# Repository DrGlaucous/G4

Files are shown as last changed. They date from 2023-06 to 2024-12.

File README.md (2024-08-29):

# "Governor" G4

This is a repo for a low-cost and feature-rich "flywheel-type" nerf blaster.

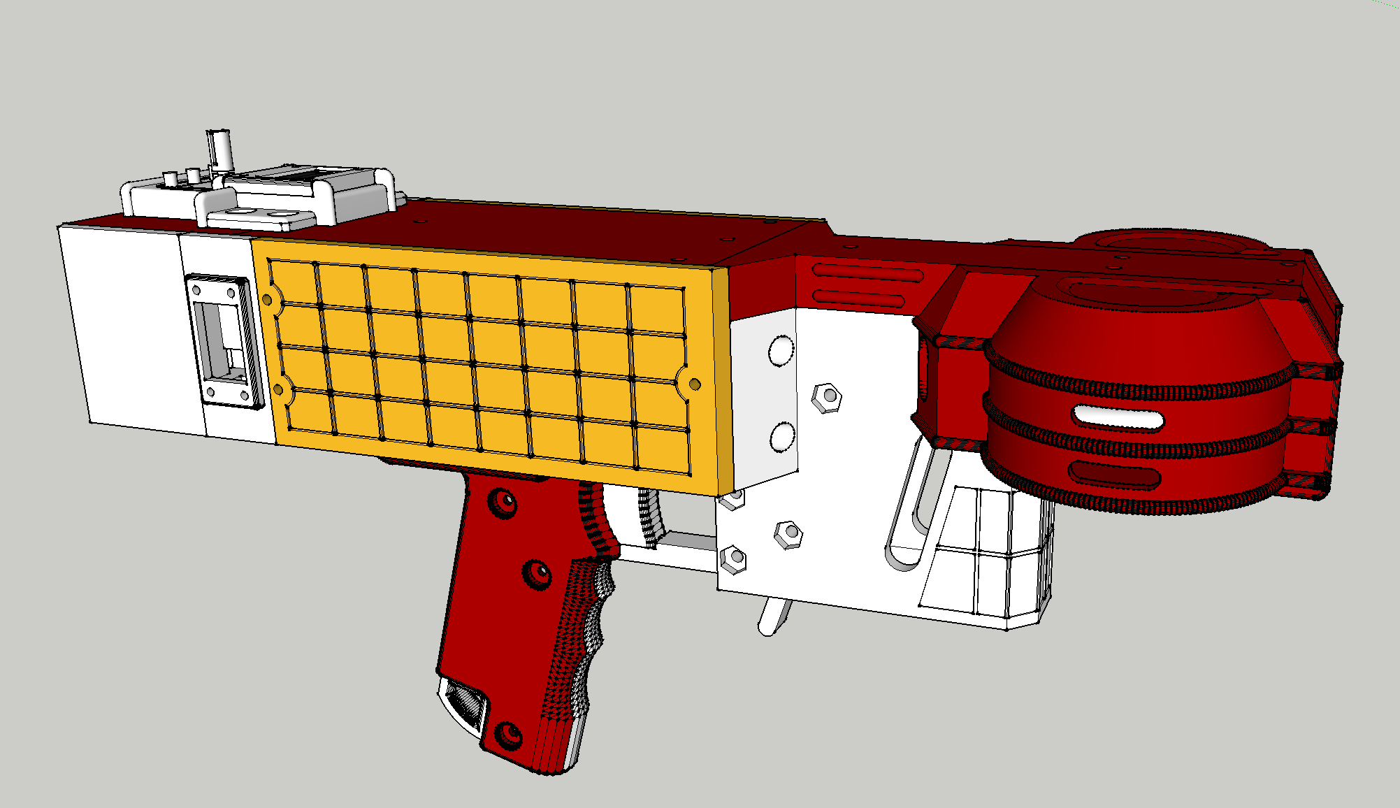
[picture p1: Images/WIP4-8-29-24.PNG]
Rendering of current iteration


Features/Speficications:
- Goal build cost < 150$
- Minimal plastic-anchored screws *(almost evertthing is secured with bolts + captive nuts)*
- Brushless motor flyhweels
- Solenoid pusher
- LCD display
- Angled talon compatability *(straight stick support planned)*
- Integrated ammo counter hardware
- Integrated chronograph hardware
- 3-5S Lipo compatable
- 6cm flywheel diameter
- ESP32 controller
- Closed-loop flywheel control (providing fixed RPM and fast spinup times)
- Through-hole electronics and soldering
- Fast decay solenoid driver

Many of these features are implemented in the G4's companion firmware, [Detty](https://github.com/DrGlaucous/DettyFW).

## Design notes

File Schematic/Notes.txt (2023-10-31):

Potential MOSFET for use with ESP32:

From Mouser:
IPP030N06NF2SAKMA1	3.05mh	3.3v thresh	1.52$	(large package only)
TK4R3A06PL,S4X	3.3mh	1.5vThresh	disp: 1.616Watt
TK4R3E06PL	3.3mh	1.5vThresh	disp: 1.616Watt (same as above, but better) 1.45$	(large package only)
IRFB3306/IRFSL3306PBF 	3.3-4.2mh	2-4vThresh	1.8$	(desirable package not stocked)
IPP019N06NF2S	1.9mh	3.3vthresh	2.1$	(large package only)
IRLB3034 ? (1.7mh), but 40vmax	$3.7$
IRFB3077	3.3mh	2-4vThresh	disp: 0.5925W with lowest (max: 2.4W)	2.2$

Pfet driver:
2N7000: Nfet, several ohm RDSon, but we won't pull much current through it.

P channel:
IPP120P04P4L03AKSA2	3.1mh	5vthresh	40vmax	$3.61

calculate dissipated power: I * I * Rds
calculate jnctn temp: multiply that by 50/60 degC/watt

at 20 volts on 1.5 ohms (solenoid), 13.33 amps flow

Choice:
DigiKey electronincs:
G040P04T - p channel (x5) $1.82/pc || https://www.digikey.com/en/products/detail/goford-semiconductor/G040P04T/19524542
or
G75P04T - p channel (x5) $1.18/pc || https://www.digikey.com/en/products/detail/goford-semiconductor/G75P04T/18768879
or
G050P03T - p channel (x5) $1.17/pc || https://www.digikey.com/en/products/detail/goford-semiconductor/G050P03T/18087996

25WA470MEFCT810X9 capacitor, 25v 470uf (x10) $0.43/pc || https://www.digikey.com/en/products/detail/rubycon/25WA470MEFCT810X9/3566890

CSD18532KCS - n channel (x5) $2.31/pc || https://www.digikey.com/en/products/detail/texas-instruments/CSD18532KCS/3661861
or cheap:
IRLB8314PBF - n channel (x5) $1.00/pc || https://www.digikey.com/en/products/detail/infineon-technologies/IRLB8314PBF/4807868 **
or (not as good...)
IRLB8748PBF 0.0068 - 2.35 - n cnannel (x5) $1.05/pc || https://www.digikey.com/en/products/detail/infineon-technologies/IRLB8748PBF/2127672
IRL7833PBF 0.0045 - 2.30 - 1.85 || https://www.digikey.com/en/products/detail/infineon-technologies/IRL7833PBF/811242

ordered:
G75P04T - pch
25WA470MEFCT810X9 - cap
IRLB8314PBF - nch

Mouser electronics (bad cap selection):
IPP030N06NF2SAKMA1- N channel (x10)
IPP120P04P4L03AKSA2 - P channel (x3)
870585375004 - Cap, 470 uf (x2) (1mc cubed footprint, 5mm leads)

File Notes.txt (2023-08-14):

Useful info:
https://randomnerdtutorials.com/esp32-pinout-reference-gpios/

how to wire and use a 2 pin IR photodiode:
https://youtu.be/_mOF1JXo1DU
https://forum.arduino.cc/t/2-pin-infrared-receiver-closed/304086/3

how u8g2 pages work:
with a 128x64 pixel display, the program will
split the bitmap into 8 horizontal slivers to be pushed
to the display, each 8 pixels tall.
Likely, this uses page rows that are a multiple of 8, so taller LCDs will have more pages

API refrence:
https://github.com/olikraus/u8g2/wiki/u8g2reference#drawbox
https://github.com/olikraus/u8g2/wiki/fntlist12

left ESC is D23
right ESC is D18

Resources for RMT:
https://docs.espressif.com/projects/esp-idf/en/latest/esp32/api-reference/peripherals/rmt.html
https://github.com/espressif/esp-idf/issues/11768
https://github.com/espressif/esp-idf/blob/master/components/driver/test_apps/rmt/main/test_rmt_rx.c#L43
https://esp32.com/viewtopic.php?t=3772
https://stackoverflow.com/questions/56127996/how-to-receive-long-data-frame-by-esp32-rmt-ringbuffer

rmt_tx_channel_config_t::with_dma //what does this do? appearently, it takes work away from the CPU...

rmt_tx_channel_config_t::io_od_mode //open drain mode
rmt_tx_channel_config_t::io_loop_back //use with this
rmt_rx_channel_config_t::io_loop_back

how I think the dshot send flow works:

every time sendThrottleValue is sent, a dhsot packet is transmitted over RMT
they do not need to happen back-to-back, but we need to keep sending at least some in order
to keep the ESC alive

how I want it to work (if data needs to be sent uber frequently):
send initial data:
attach callback to RMT loopback pin, set it to call when it gets 32 bits (the 16 we send and the 16 we get back)
ship this data out and send the next RMT packet...

or...

send a packet and quick enable a callback to the RMT RX channel
callback set for 16 bits (because it will be started after we send the first packet)

on callback, we cache the data and disable the callback

receiver callback gets signals between an min and max timescale
signals larger than these are considered stop bits
when a stop bit is hit, rmt_receive() must be called a second time

so...
send MY data, call rmt_receive() to prepare for data coming back
when callback triggers, relocate data to buffer to get gotten later, 

repeat as needed (still don't know if the user tells the RMT each time they want to send, or
if it does it automatically on a timer)

if it is the former, we put the RX prep at the end of the function.
if it is the latter, we set up an TX callback when it finishes transmission.

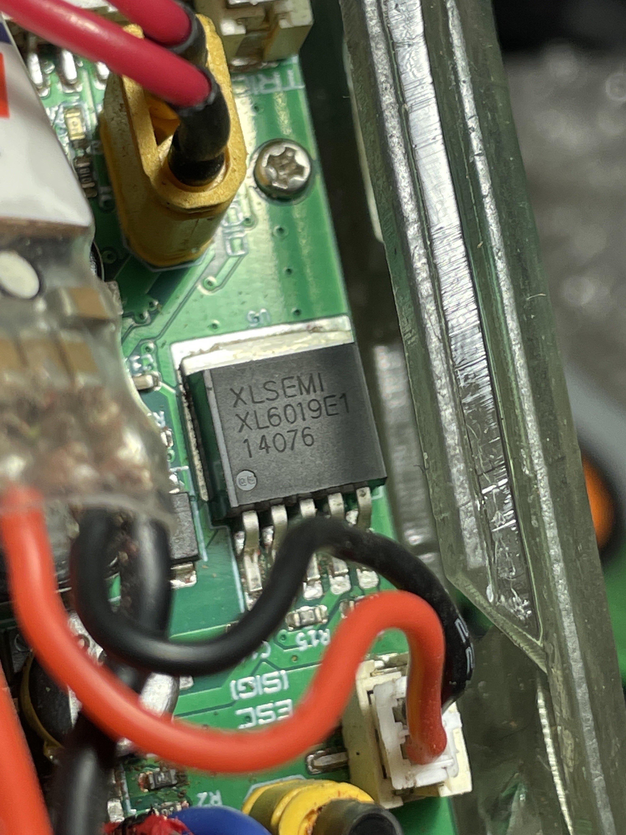
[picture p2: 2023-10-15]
Images/BoostedSolenoid.jpg

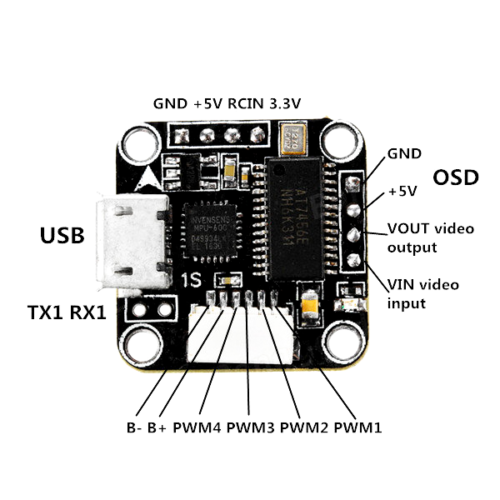
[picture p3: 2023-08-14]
Images/MicroM3_FlightController/s-l500.png

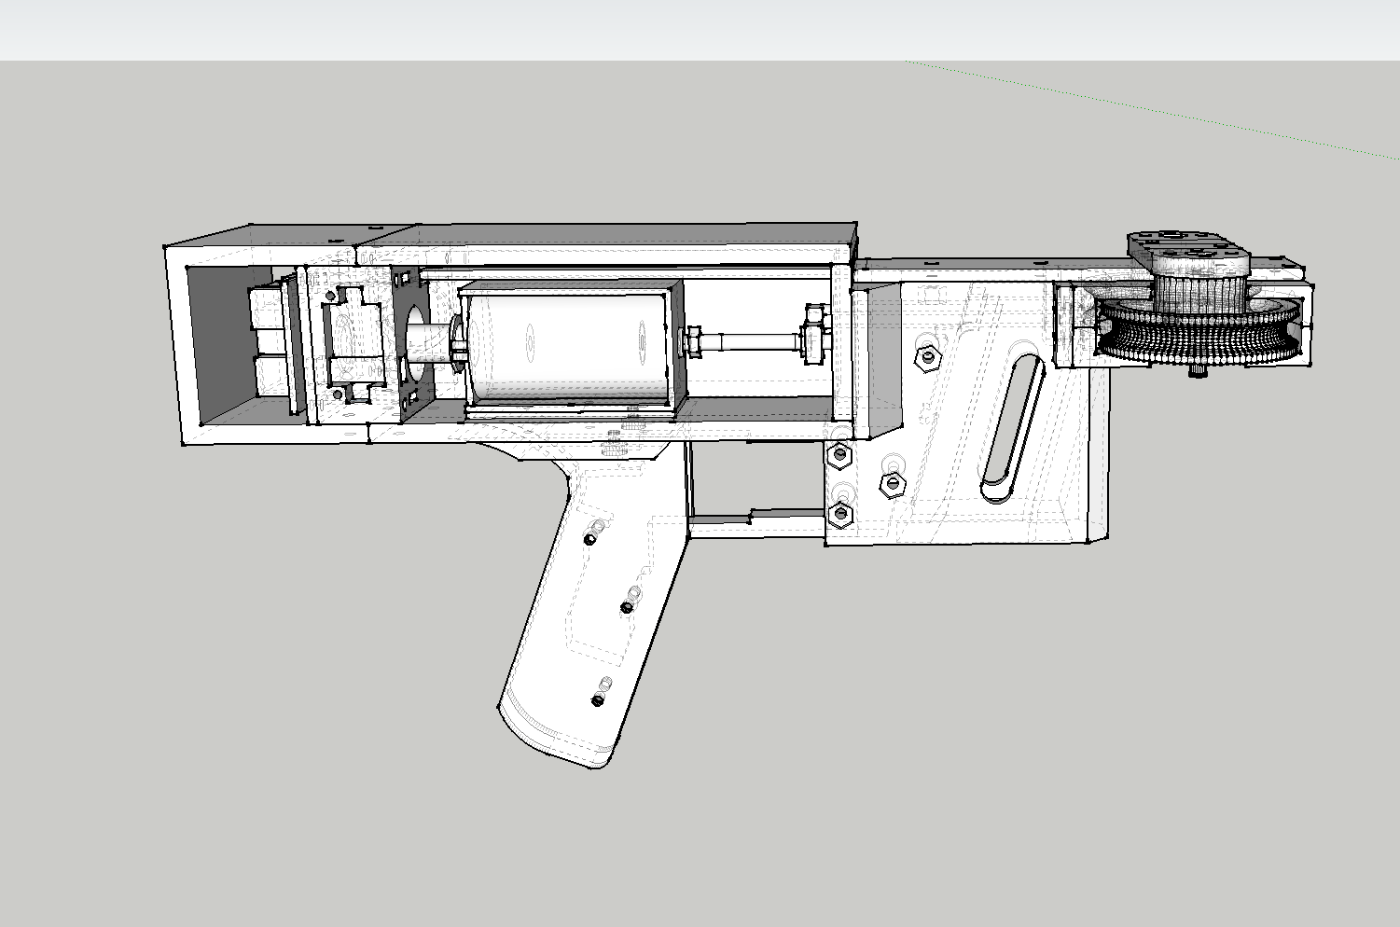
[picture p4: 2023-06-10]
Images/WIP1-6-7-23.PNG

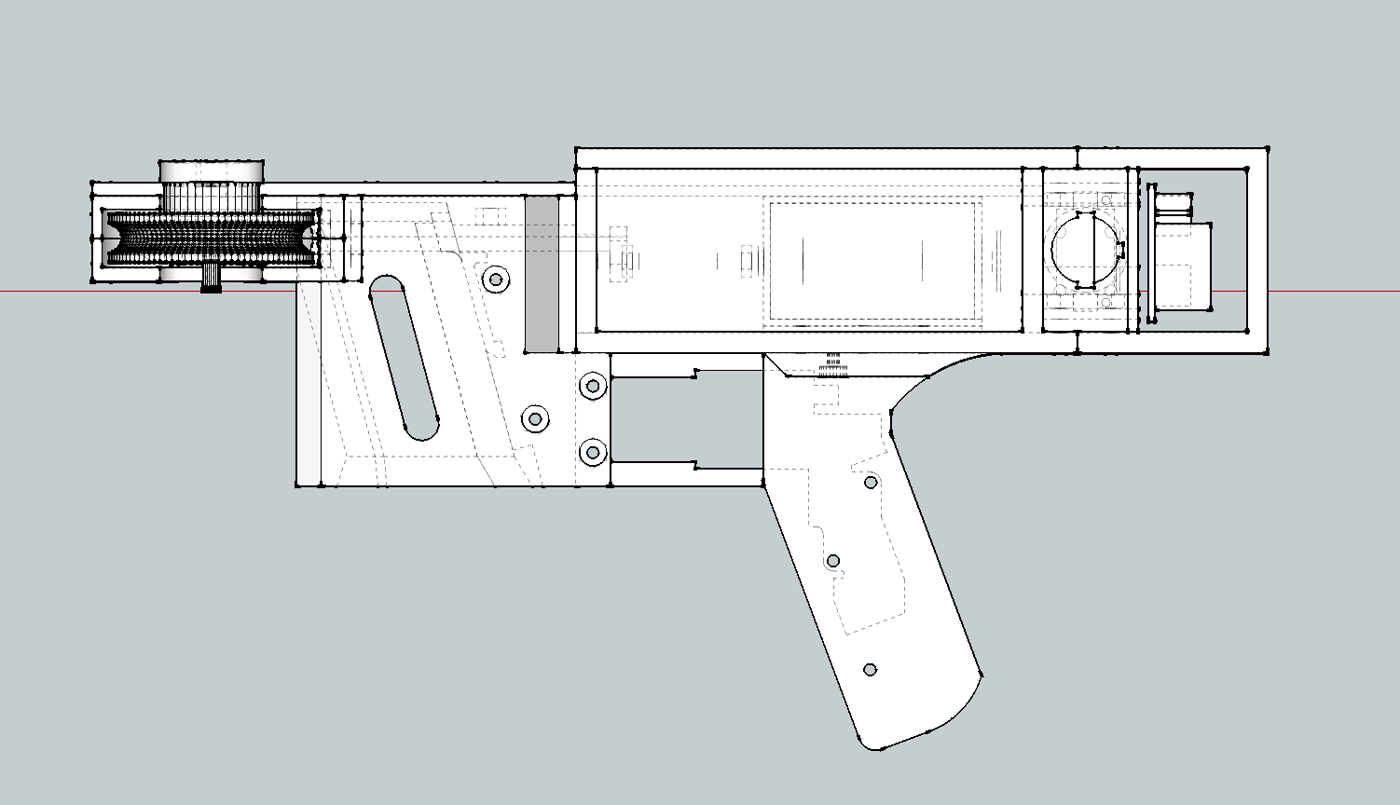
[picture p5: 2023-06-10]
Images/WIP3-6-7-23.PNG

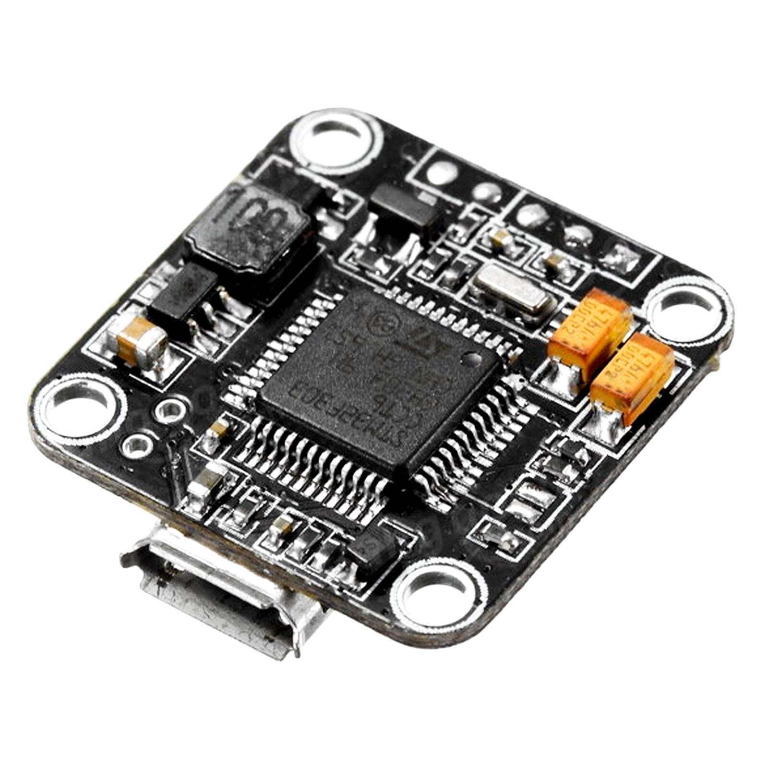
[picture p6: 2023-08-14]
Images/MicroM3_FlightController/s-l1600.jpg

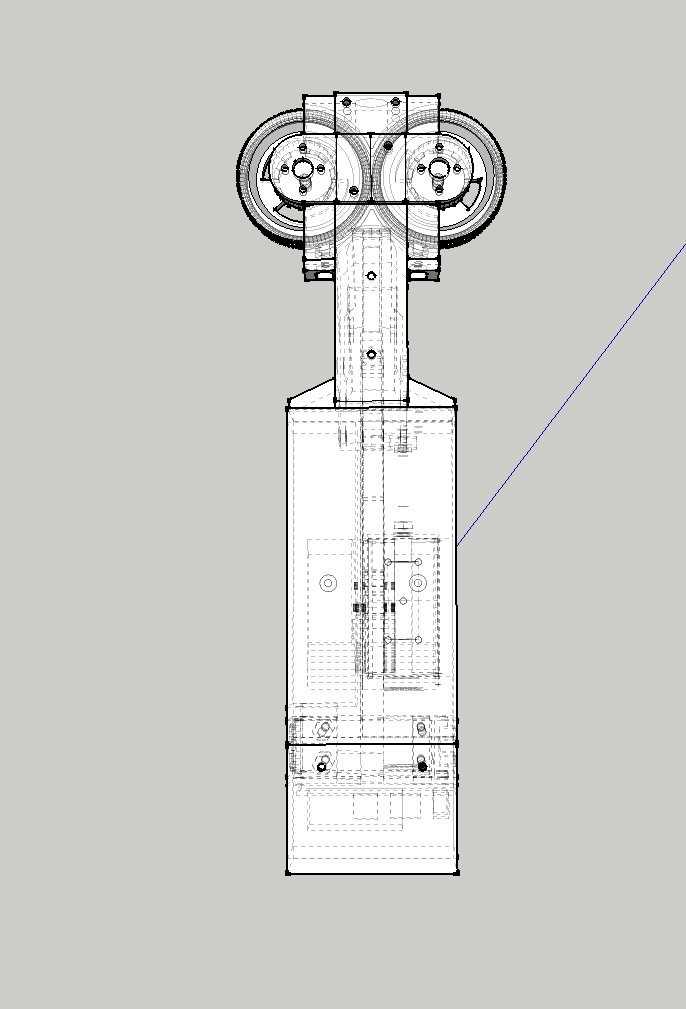
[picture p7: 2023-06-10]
Images/WIP2-6-7-23.PNG

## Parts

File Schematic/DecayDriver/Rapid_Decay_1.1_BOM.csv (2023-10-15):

ID | Name | Designator | Footprint | Quantity | Manufacturer Part | Manufacturer | Supplier | Supplier Part | Price
1 | BAT | BAT | BATTERY 20X10MM 2 PADS | 1 |  |  | LCSC | C49661 | 0.035
2 | HSP80P10 | Q1 | TO-220-3_L10.0-W4.5-P2.54-L | 1 | HSP80P10 | HUASHUO | LCSC | C845619 | 1.411
3 | SWD050R95E8S | Q3,Q4 | TO-252-3_L6.6-W6.1-P4.58-LS10.1-BR-1 | 2 | SWD050R95E8S | Samwin(芯派) | LCSC | C5151846 | 0.331
4 | 10K | R10K,RESI10K | R1206 | 2
5 | 100 | R100,R100OHM | R1206 | 2
6 | 10k | RES10K | R1206 | 1
7 | ES1D-DO214AC | SCH-DIODE,SCHO-DIODE | SMA_L4.3-W2.6-LS5.2-RD | 2 | ES1D-DO214AC |  | LCSC | C9900005800
8 | Solenoid Power Cables | SOLENOID1 | SOLENOID 2PADS 10X7MM TOTAL | 1 |  |  |  | C124375 | 0.022
9 | Solenoid drv | SOLENOID-DVR | HDR-TH-2PFV-P2.54-D0.8 | 1 |  |  | LCSC | C49661 | 0.035

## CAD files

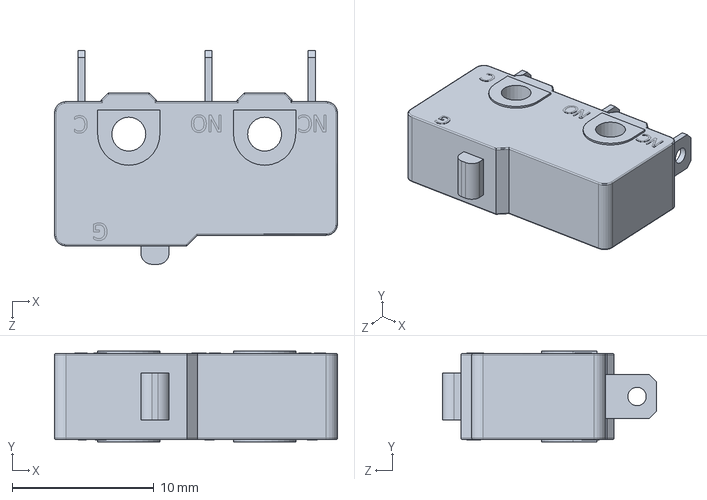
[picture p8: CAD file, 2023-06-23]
CAD/Reference/Microswitch.SLDPRT
20.0 x 6.40 x 15.1 mm

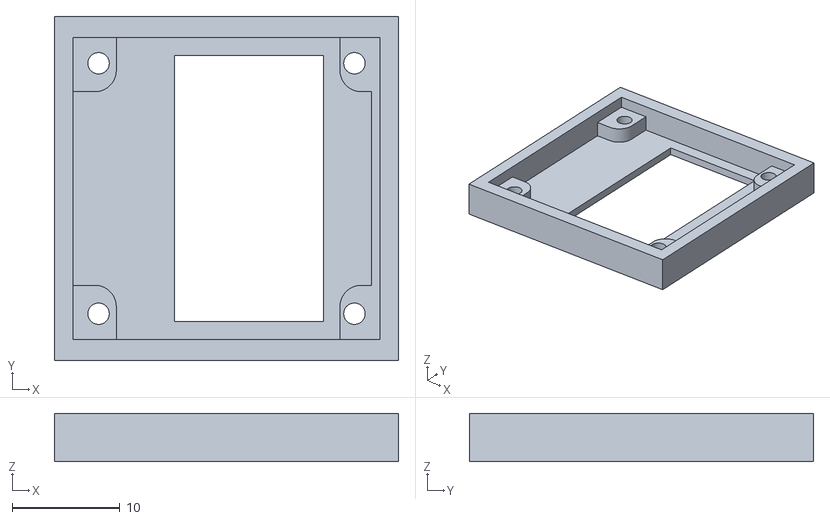
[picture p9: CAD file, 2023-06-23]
CAD/STL/Back/DispPan/PannelCap.stl
32.0 x 32.0 x 4.50

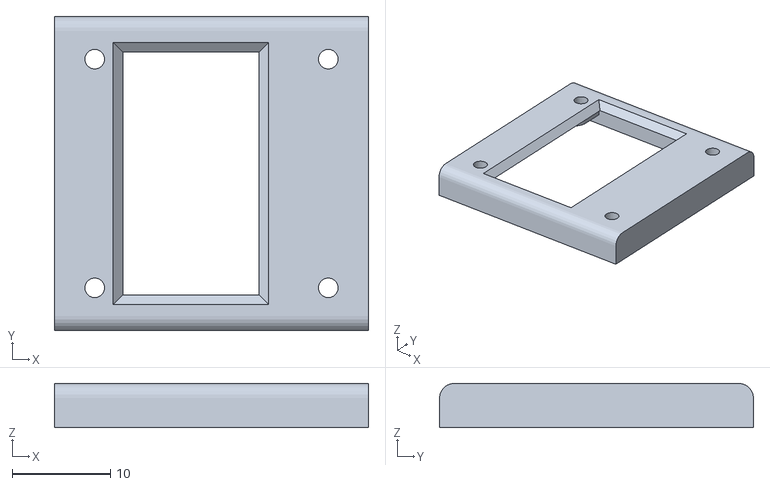
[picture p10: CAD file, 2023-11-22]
CAD/STL/Back/ScreenCap.stl
32.0 x 32.0 x 4.50

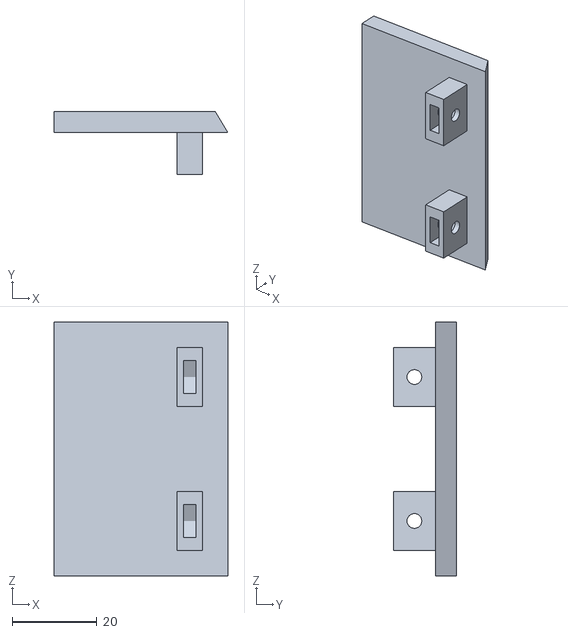
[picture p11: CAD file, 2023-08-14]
CAD/STL/Back/V1Noose/BackSideCover.stl
41.0 x 15.0 x 60.0

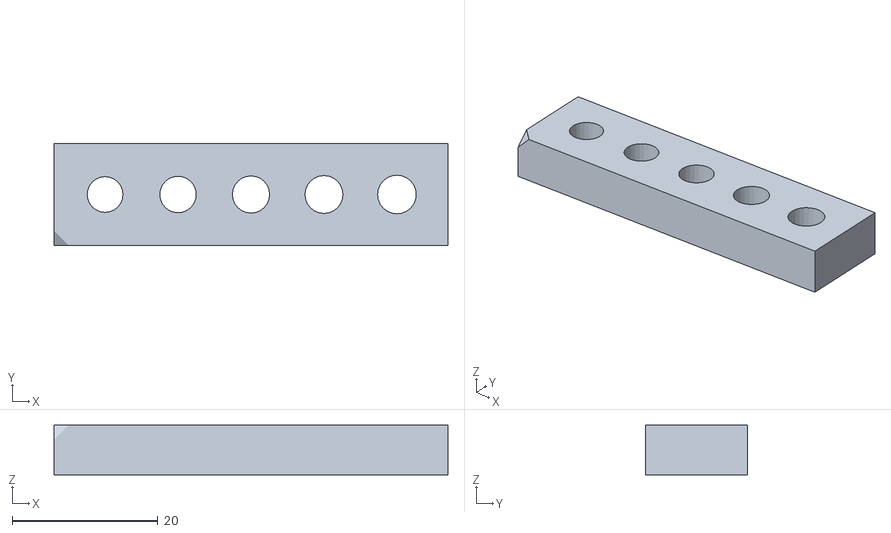
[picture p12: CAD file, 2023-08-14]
CAD/STL/FlywheelHoleSizeTest.stl
54.0 x 14.0 x 6.80

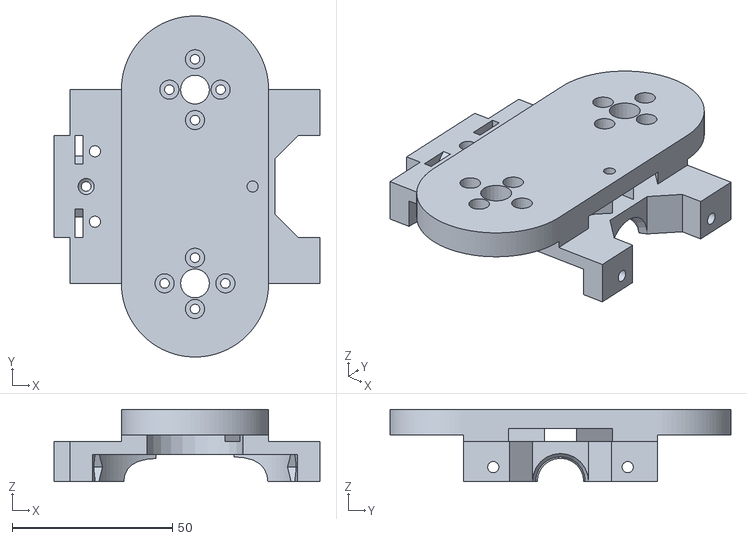
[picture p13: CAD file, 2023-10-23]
CAD/STL/Front/Depricated/FlywheelCageMotorSide.stl
83.0 x 106.5 x 22.5

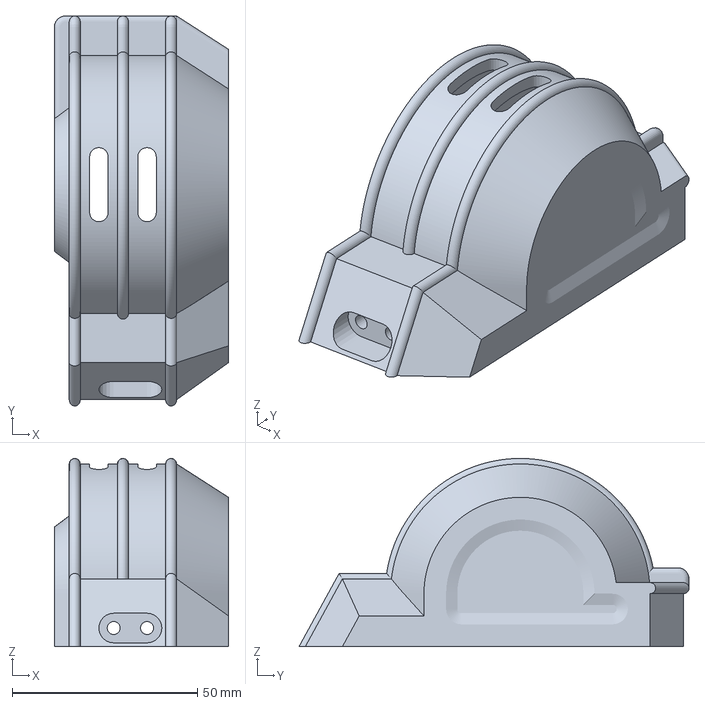
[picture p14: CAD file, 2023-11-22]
CAD/STL/Front/WheelCowlLeft.3mf
47.0 x 105.2 x 50.8 mm

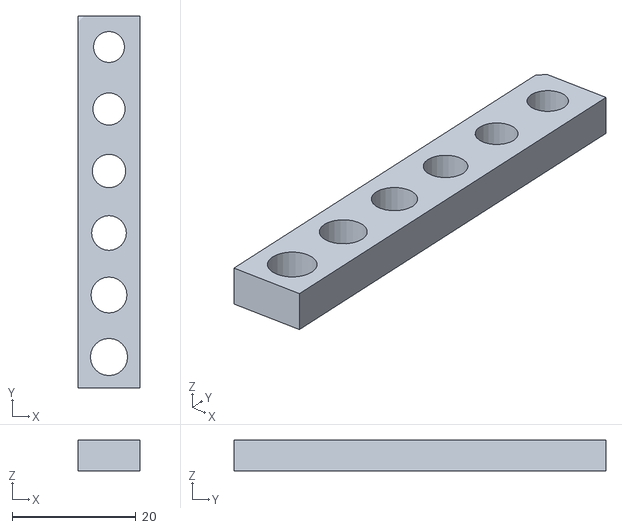
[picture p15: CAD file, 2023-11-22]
CAD/STL/Tests/FlywheelShaftTest.stl
10.0 x 60.0 x 5.00

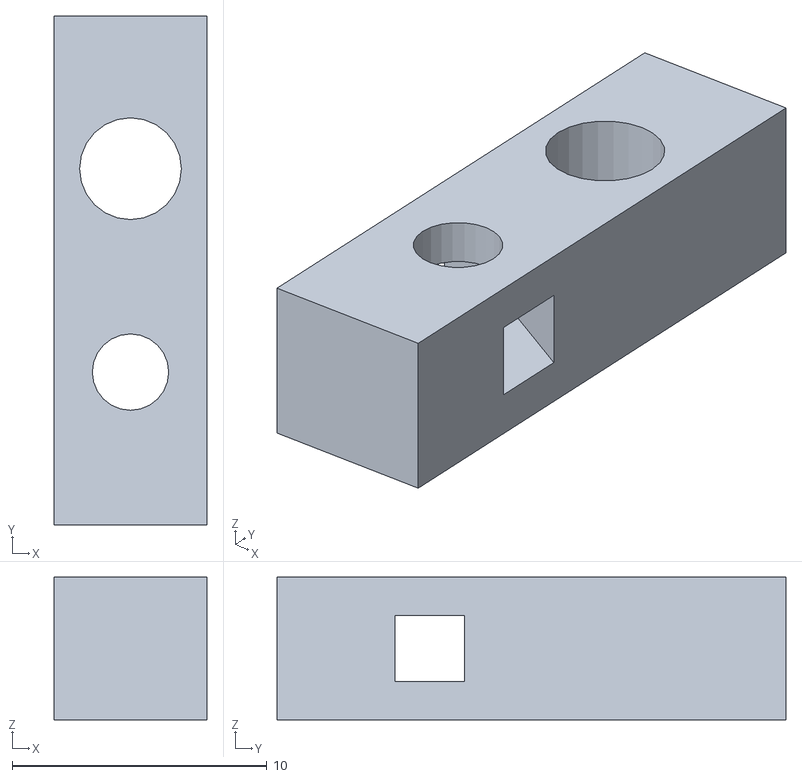
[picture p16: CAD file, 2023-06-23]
CAD/Tests/M3Test.stl
6.00 x 20.0 x 5.60

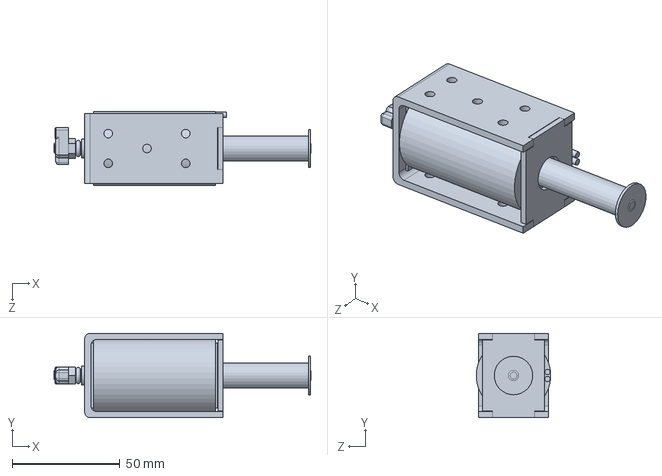
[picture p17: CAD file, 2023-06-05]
CAD/Reference/Solenoid.SLDPRT
119.0 x 39.1 x 34.4 mm

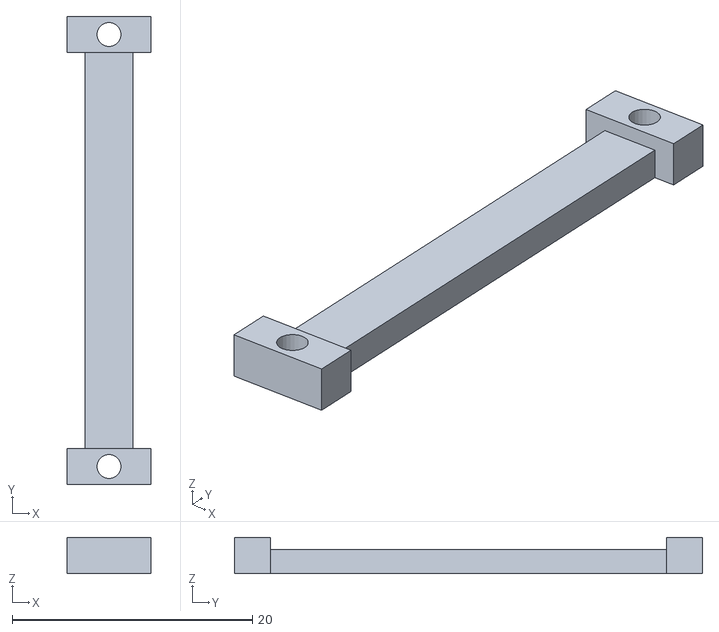
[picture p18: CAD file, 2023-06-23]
CAD/STL/Back/DispPan/ButtonHolder.stl
7.00 x 39.0 x 3.00

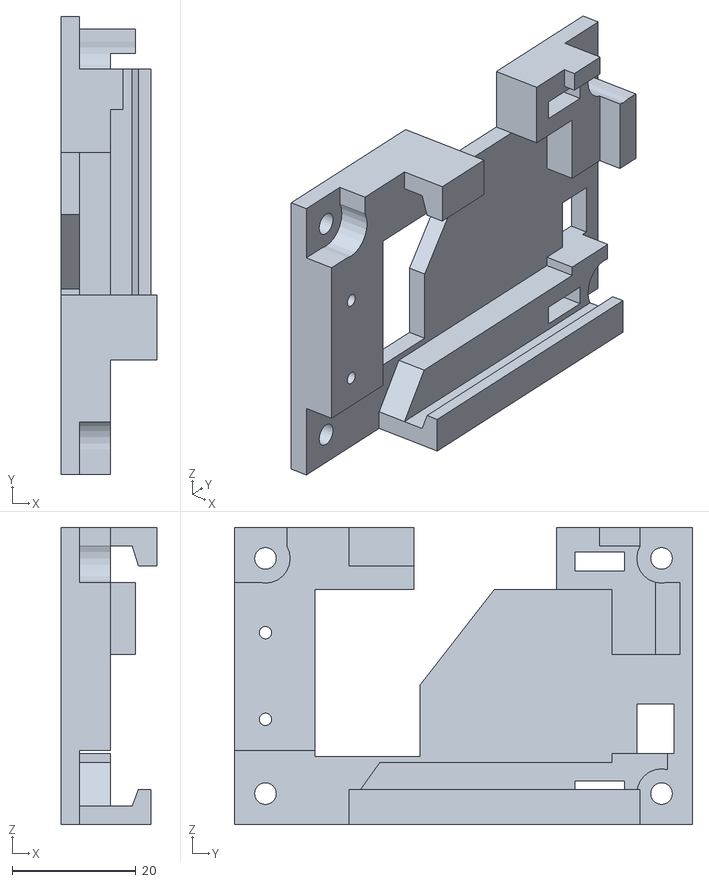
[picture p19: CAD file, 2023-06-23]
CAD/STL/Back/V1Noose/SwitchboardBackplate.stl
15.5 x 74.0 x 48.0

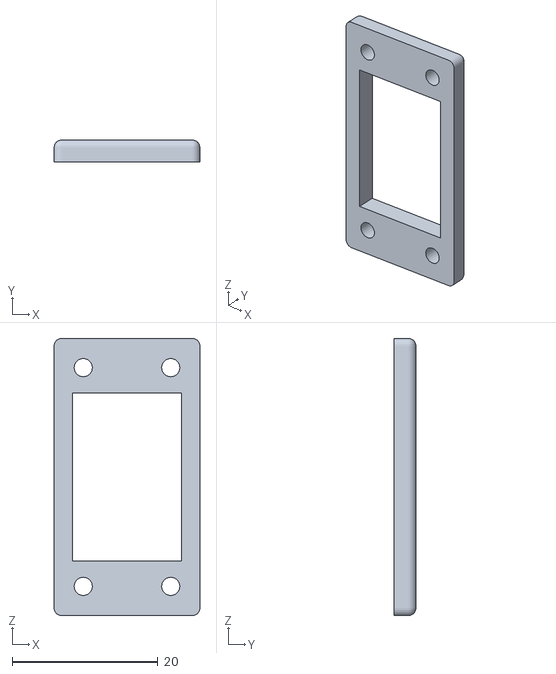
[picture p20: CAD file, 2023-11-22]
CAD/STL/Back/VoltmeterCover.stl
20.0 x 3.00 x 38.0

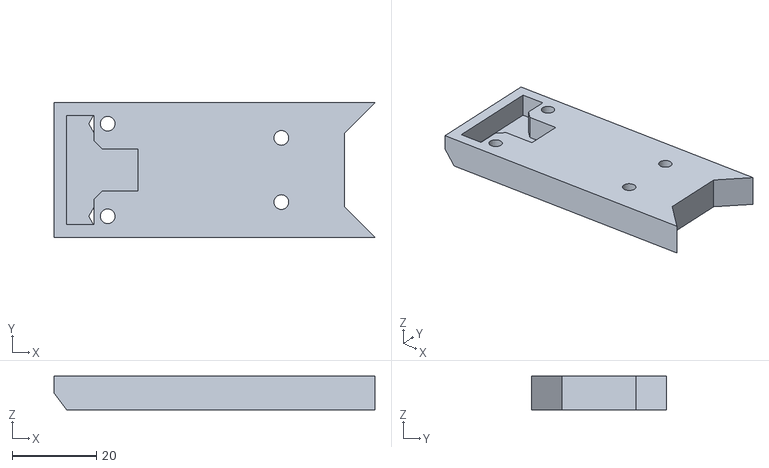
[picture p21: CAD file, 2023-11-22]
CAD/STL/Front/BottomLEDCap.stl
76.3 x 32.0 x 8.00

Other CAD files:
CAD/STL/Front/Depricated/FlywheelCageMotorSide_SLICE.3mf
CAD/STL/InternalPartsPlate.stl
CAD/STL/Tests/CoverProfileTest.stl
CAD/STL/Back/DispPan/PannelBase.stl
CAD/Reference/Microswitch.STL
CAD/Reference/Solenoid.STL
CAD/STL/Back/BatteryTray.stl
CAD/STL/Back/CircuitWall.stl
CAD/STL/Back/ControlPanel.stl
CAD/STL/Back/DartFinger.3mf
CAD/STL/Back/DartFinger.stl
CAD/STL/Back/FrontSideCover.stl
CAD/STL/Back/HandleCore.stl
CAD/STL/Back/HandleLeft.stl
CAD/STL/Back/HandleRight.stl
CAD/STL/Back/MagReleaseButton2.stl
CAD/STL/Back/NooseBackCover.stl
CAD/STL/Back/NooseMount.stl
CAD/STL/Back/SolenoidFloor.stl
CAD/STL/Back/SolenoidRoof.stl
CAD/STL/Back/SolenoidWallBack.stl
CAD/STL/Back/SolenoidWallFront.stl
CAD/STL/Back/Top.stl
CAD/STL/Back/Trigger.stl
CAD/STL/Back/V1Noose/ElectronicsCap.stl
CAD/STL/Back/V1Noose/Switchboard.stl
CAD/STL/Front/CageHalf.stl
CAD/STL/Front/CageMotorMount.stl
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

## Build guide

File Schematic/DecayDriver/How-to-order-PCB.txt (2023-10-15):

How to Order PCB

Please refer to:
https://docs.easyeda.com/en/PCB/Order-PCB

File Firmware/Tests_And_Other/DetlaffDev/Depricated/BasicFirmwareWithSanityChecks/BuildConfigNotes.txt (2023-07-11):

The root ini file sets up the default config.
this config is called [platformio]

it specifies:
src_dir -- source directory
boards_dir -- board directory (holds upload settings for each board)
default_envs -- what boiard to choose by default
include_dir -- include a subdirectory to build off (mainly good for marlin, which is massive)
extra_configs -- specifies some ini files where parts of the sources should be added or removed based on what type of board thei firmware is being uploaded to

default_src_filter -- specifies what files and directories should be added or removed from the build list by default
this list is changed in the subdirectories

each subdirectory is divided by processor, and further by individual board according to their features

the ESP32's memory can be partitioned accoridng to an partition table loaded from a CSV

the marlin directroy has an config.ini file,
this file specifies printer settings in a slightly less user-friendly way than configuration.h
this is probably used for re-configuring files on the fly after the firmware has been uploaded...

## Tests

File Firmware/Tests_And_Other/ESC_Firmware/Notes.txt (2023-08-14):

FC firmware version:
# version
# Betaflight/OMNIBUS 3.1.0 Dec  2 2016 / 16:47:34 (01968ff)

STM32F303

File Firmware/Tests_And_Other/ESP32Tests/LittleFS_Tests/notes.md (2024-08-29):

To upload files, speficy `board_build.filesystem = littlefs` in the platformIO config.

Place files for upload into the `./data` directory
and run the `board_name>platform>Upload Filesystem Image` task to push this stuff to the internal littlefs directory

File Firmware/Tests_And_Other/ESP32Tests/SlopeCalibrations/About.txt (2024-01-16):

Used to test dshot voltage-slope curves
and other real-world relations for Detty

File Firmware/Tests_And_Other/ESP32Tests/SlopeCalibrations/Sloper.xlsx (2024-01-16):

ADC Read | Real Voltage | Fake Voltage
2113 | 28.83 | 32.62
1412 | 20 | 21.8
1261 | 18.01 | 19.47
1099 | 16 | 16.96
934 | 14 | 14.42
779 | 12 | 12.3
620 | 10 | 9.56
546 | 9 | 8.43

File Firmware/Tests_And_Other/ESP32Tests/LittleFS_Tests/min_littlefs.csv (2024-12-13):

# Name | Type | SubType | Offset | Size | Flags
nvs | data | nvs | 0x9000 | 0x5000
otadata | data | ota | 0xe000 | 0x2000
app0 | app | ota_0 | 0x10000 | 0x1E0000
app1 | app | ota_1 | 0x1F0000 | 0x1E0000
spiffs | data | spiffs | 0x3D0000 | 0x30000

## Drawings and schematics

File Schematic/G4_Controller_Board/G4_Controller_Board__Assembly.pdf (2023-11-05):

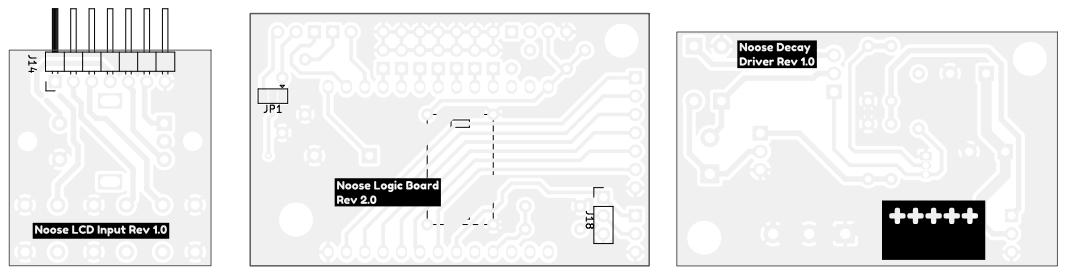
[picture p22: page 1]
D Date: KiCad; kicad; 7.0.8 Size: A4; Rev: 2.0; Id: 1/1 Title: Noose Blaster Controller File: G4_Controller_Board.kicad_pcb Sheet: Designed; for the G4 Governor J18

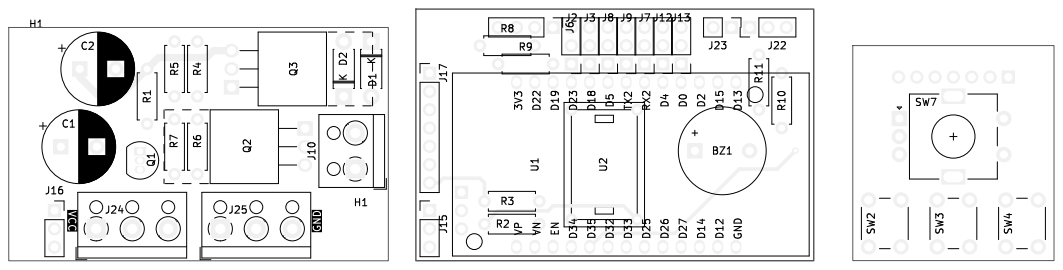
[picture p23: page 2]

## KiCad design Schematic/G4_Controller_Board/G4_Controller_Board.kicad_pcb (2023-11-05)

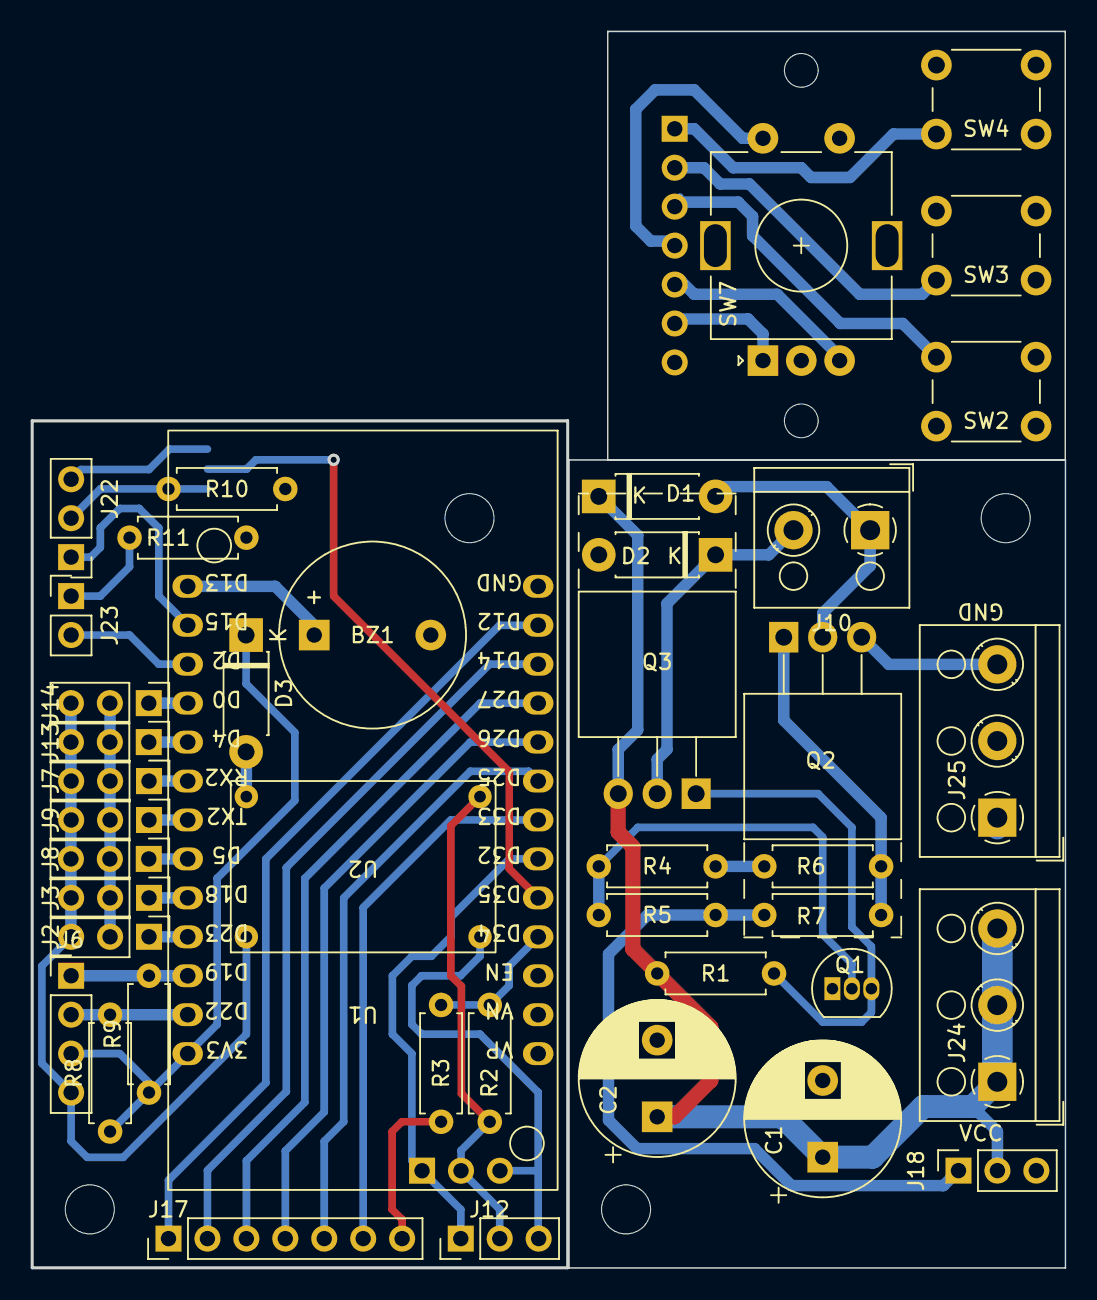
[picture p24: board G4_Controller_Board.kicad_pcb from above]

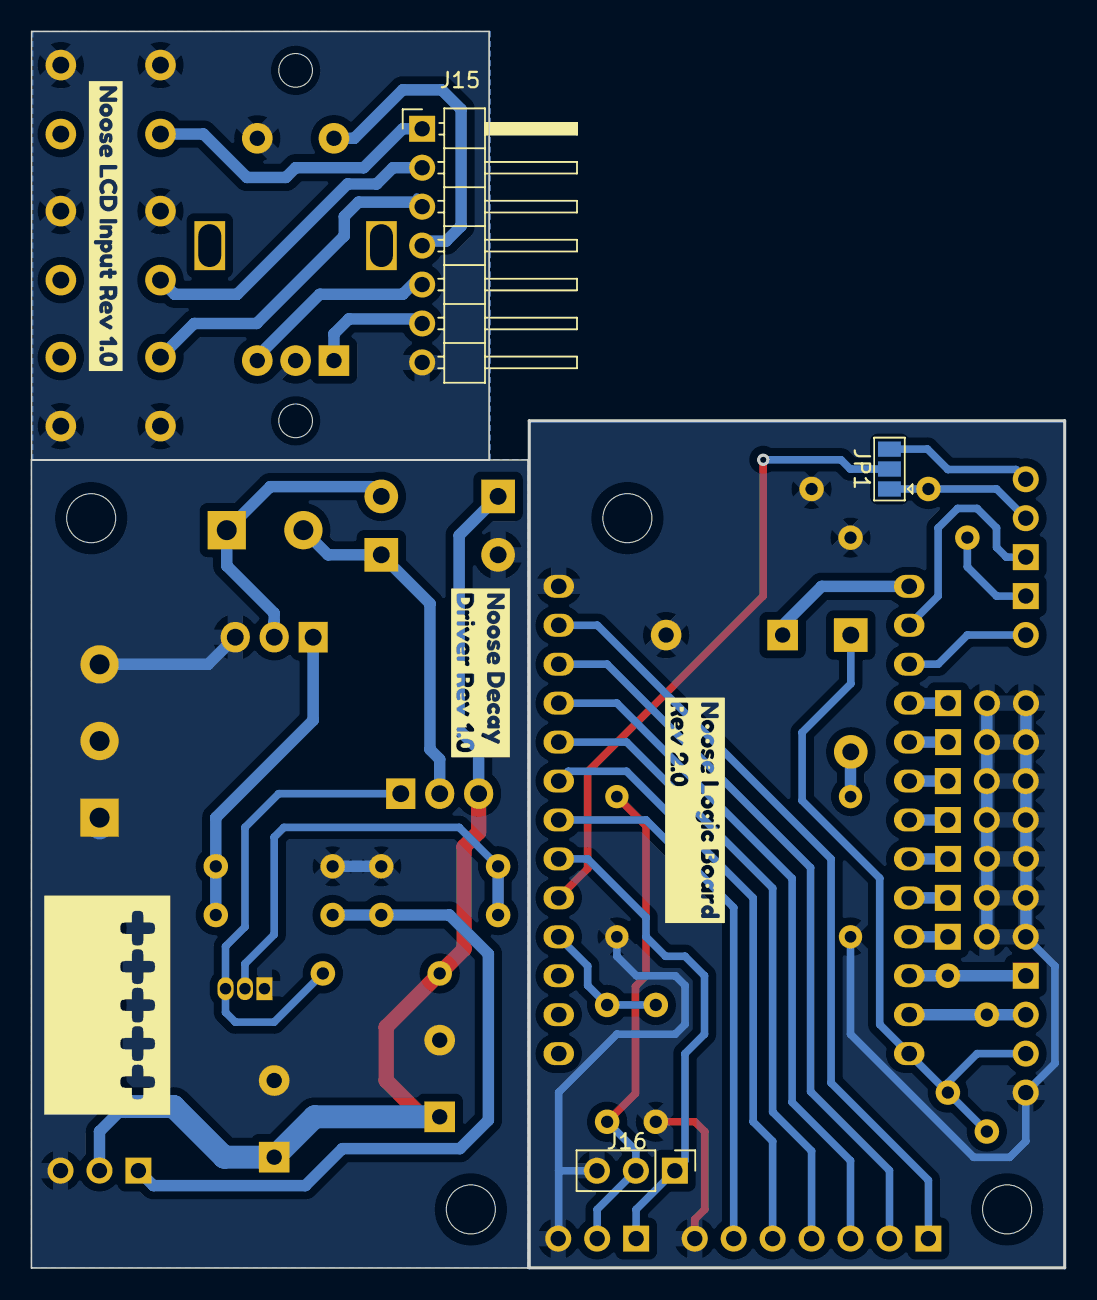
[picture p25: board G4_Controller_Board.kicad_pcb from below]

Board: 2 copper layers, 67.4 x 80.7 mm, 55 parts (7 on the bottom side), 33 nets.

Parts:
BZ1: Buzzer; Buzzer_12x9.5RM7.6
C1, C2: 470uF; CP_Radial_D10.0mm_P5.00mm
D1, D2, D3: 1N4001; D_DO-41_SOD81_P7.62mm_Horizontal
H1, H1#2, H1#3, H1#4: MountingHole; MountingHole_3.2mm_M3
H1#5, H1#6: MountingHole; MountingHole_2.2mm_M2
J2: ESC Right; PinHeader_1x03_P2.54mm_Vertical
J3: ESC Left; PinHeader_1x03_P2.54mm_Vertical
J6: I2C Out; PinHeader_1x04_P2.54mm_Vertical
J7: Rev Trigger (Optional); PinHeader_1x03_P2.54mm_Vertical
J8: Fire Trigger; PinHeader_1x03_P2.54mm_Vertical
J9: Magazine Removal Trigger; PinHeader_1x03_P2.54mm_Vertical
J10: Solenoid; TerminalBlock_RND_205-00001_1x02_P5.00mm_Horizontal
J12, J16: Board Interconnect; PinHeader_1x03_P2.54mm_Vertical
J13: SolenoidTrig A (Optional); PinHeader_1x03_P2.54mm_Vertical
J14: SolenoidTrig B (Optional); PinHeader_1x03_P2.54mm_Vertical
J15: Board Interconnect; PinHeader_1x07_P2.54mm_Horizontal
J17: Board Interconnect; PinHeader_1x07_P2.54mm_Vertical
J18: Board Interconnect; PinSocket_1x03_P2.54mm_Vertical
J22: IR LED Rec.; PinHeader_1x03_P2.54mm_Vertical
J23: IR LED Emitter; PinHeader_1x02_P2.54mm_Vertical
J24: Positive BUS; TerminalBlock_RND_205-00002_1x03_P5.00mm_Horizontal
J25: Negative BUS; TerminalBlock_RND_205-00002_1x03_P5.00mm_Horizontal
JP1: Jumper_3_Bridged12; SolderJumper-3_P1.3mm_Open_Pad1.0x1.5mm
Q1: 2N7000; TO-92_Inline
Q2: Q_NMOS_GDS; TO-220-3_Horizontal_TabUp
Q3: Q_PMOS_GDS; TO-220-3_Horizontal_TabUp
R1, R4, R6: 10KR; R_Axial_DIN0207_L6.3mm_D2.5mm_P7.62mm_Horizontal
R2: 150k Ohm; R_Axial_DIN0207_L6.3mm_D2.5mm_P7.62mm_Horizontal
R3: 10k Ohm; R_Axial_DIN0207_L6.3mm_D2.5mm_P7.62mm_Horizontal
R5, R7: 100R; R_Axial_DIN0207_L6.3mm_D2.5mm_P7.62mm_Horizontal
R8, R9: 2.4k Ohm; R_Axial_DIN0207_L6.3mm_D2.5mm_P7.62mm_Horizontal
R10: 10K Ohm; R_Axial_DIN0207_L6.3mm_D2.5mm_P7.62mm_Horizontal
R11: 90 Ohm; R_Axial_DIN0207_L6.3mm_D2.5mm_P7.62mm_Horizontal
SW2: Preset A; SW_PUSH_6mm_H13mm
SW3: Preset B; SW_PUSH_6mm_H13mm
SW4: Preset C; SW_PUSH_6mm_H13mm
SW7: RotaryEncoder_Switch; RotaryEncoder_Alps_EC11E-Switch_Vertical_H20mm
U1: ESP32-LOLIN32-Lite
U2: Mini360
kibuzzard-654684EA: G***; kibuzzard-654684EA
kibuzzard-654685C2: G***; kibuzzard-654685C2
kibuzzard-654685F2: G***; kibuzzard-654685F2
kibuzzard-65468392: G***; kibuzzard-65468392

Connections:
+3V3: D3.1 (K), J6.3, R8.1, R9.1, U1.40 (3V3)
+12V: C1.1, C2.1, D1.1 (K), J12.2, J16.2, J18.2, J24.1, J24.2, J24.3, Q3.3 (S), R1.1, R2.2, U2.2 (IN)
/Battery Reader: R2.1, R3.2, U1.10 (D34)
/Buzzer: BZ1.1 (-), U1.20 (D13)
/ESC Left: J3.1, U1.35 (D18)
/ESC Right: J2.1, U1.36 (D23)
/Encoder A: J15.6, J17.6, SW7.A, U1.13 (D33)
/Encoder B: J15.5, J17.5, SW7.B, U1.14 (D25)
/Encoder Switch: J15.4, J17.4, SW7.S2, U1.15 (D26)
/FireTrg: J8.1, U1.34 (D5)
/High Side Driver: Q1.2 (G), R4.2, R5.1
/IR Emitter: J23.2, U1.22 (D2)
/IR Rec. Supply: J22.1, U1.21 (D15)
/IR Reciever: JP1.2 (C), U1.11 (D35)
/Low Side Driver: Q2.1 (G), R6.2, R7.1
/MagTrg: J9.1, U1.27 (TX2/D17)
/Preset A: J15.3, J17.3, SW2.2, U1.16 (D27)
/Preset B: J15.2, J17.2, SW3.1, U1.17 (D14)
/Preset C: J15.1, J17.1, SW4.1, U1.18 (D12)
/Pusher Pin: J12.1, J16.1, J18.1, R5.2, R7.2, U1.12 (D32)
/RevTrg: J7.1, U1.25 (RX2/D16)
/SCL/SCK (Clock): J6.2, R8.2, U1.39 (D22)
/SDA/SDI (Data): J6.1, R9.2, U1.38 (D19)
/SOLENOID_A: D1.2 (A), J10.1, Q2.2 (D)
/SOLENOID_B: D2.1 (K), J10.2, Q3.2 (D)
/SolTrig A: J13.1, U1.24 (D4)
/SolTrig B: J14.1, U1.23 (D0)
GND: BZ1.2 (+), C1.2, C2.2, D2.2 (A), J2.2, J2.3, J3.2, J3.3, J6.4, J7.2, J7.3, J8.2, J8.3, J9.2, J9.3, J12.3, J13.2, J13.3, J14.2, J14.3, J15.7, J16.3, J17.7, J18.3, J25.1, J25.2, J25.3, Q1.1 (S), Q2.3 (S), R3.1, R4.1, R6.1, R10.1, R11.1, SW2.1, SW3.2, SW4.2, SW7.C, SW7.S1, U1.19 (GND), U2.1 (GND), U2.3 (GND)
unnamed: D3.2 (A), U2.4 (OUT)
unnamed: J22.2, JP1.1 (A), R10.2
unnamed: J22.3, JP1.3 (B)
unnamed: J23.1, R11.2
unnamed: Q1.3 (D), Q3.1 (G), R1.2

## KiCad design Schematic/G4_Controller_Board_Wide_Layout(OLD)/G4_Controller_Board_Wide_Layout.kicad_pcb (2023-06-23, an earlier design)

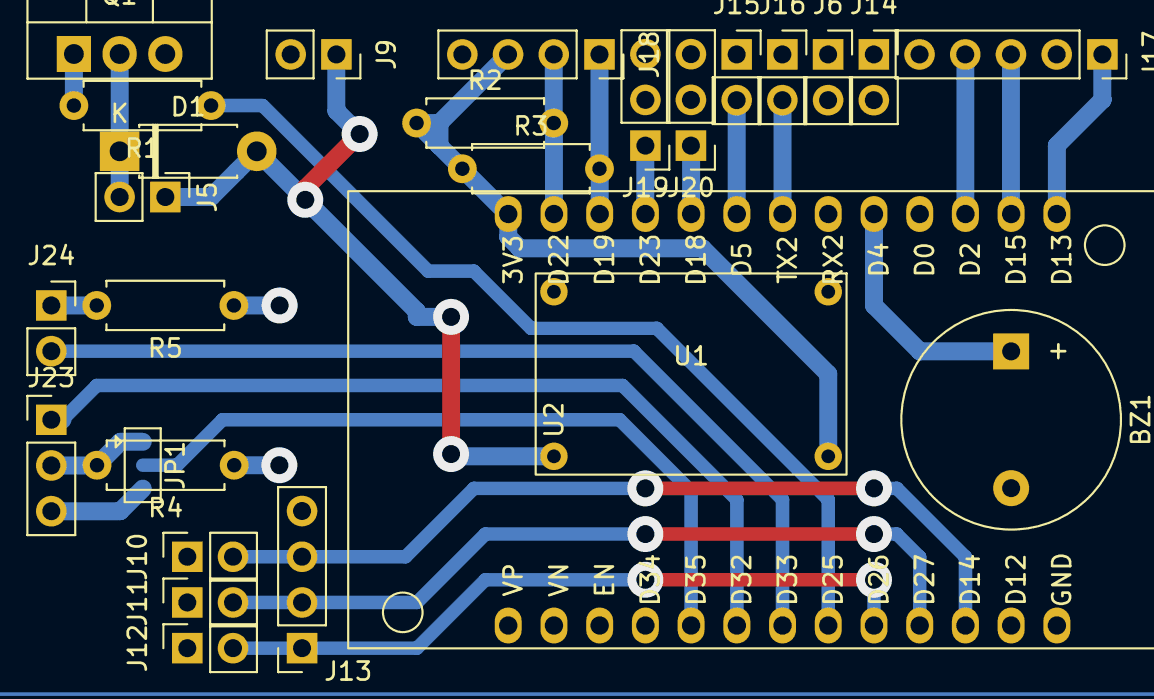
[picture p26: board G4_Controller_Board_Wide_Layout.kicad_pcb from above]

Board: 2 copper layers, 27 parts (0 on the bottom side), 25 nets.

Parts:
BZ1: Buzzer; Buzzer_12x9.5RM7.6
D1: IN4001; D_DO-41_SOD81_P7.62mm_Horizontal
J5: Solenoid; PinHeader_1x02_P2.54mm_Vertical
J6, J15: Fire Trigger; PinSocket_1x02_P2.54mm_Vertical
J9: 12 Volts In; PinSocket_1x02_P2.54mm_Vertical
J10: Preset A; PinSocket_1x02_P2.54mm_Vertical
J11: Preset B; PinSocket_1x02_P2.54mm_Vertical
J12: Preset C; PinSocket_1x02_P2.54mm_Vertical
J13: Combined Preset Connector; PinSocket_1x04_P2.54mm_Vertical
J14: Rev Trigger (Optional); PinSocket_1x02_P2.54mm_Vertical
J16: Magazine Removal Trigger; PinSocket_1x02_P2.54mm_Vertical
J17: Rotary Encoder; PinSocket_1x05_P2.54mm_Vertical
J18: I2C Out; PinSocket_1x04_P2.54mm_Vertical
J19: ESC Right; PinHeader_1x03_P2.54mm_Vertical
J20: ESC Left; PinHeader_1x03_P2.54mm_Vertical
J23: IR LED Rec.; PinHeader_1x03_P2.54mm_Vertical
J24: IR LED Emitter; PinSocket_1x02_P2.54mm_Vertical
JP1: Jumper_3_Bridged12; SolderJumper-3_P1.3mm_Open_Pad1.0x1.5mm
Q1: IRF540N; TO-220-3_Vertical
R1: 220; R_Axial_DIN0207_L6.3mm_D2.5mm_P7.62mm_Horizontal
R2, R3: 2.4k Ohm; R_Axial_DIN0207_L6.3mm_D2.5mm_P7.62mm_Horizontal
R4: 10K Ohm; R_Axial_DIN0207_L6.3mm_D2.5mm_P7.62mm_Horizontal
R5: 90 Ohm; R_Axial_DIN0207_L6.3mm_D2.5mm_P7.62mm_Horizontal
U1: Mini360
U2: ESP32-LOLIN32-Lite

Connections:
+3V3: J18.3, R2.1, R3.1, U1.4 (OUT), U2.40 (3V3)
+12V: D1.2 (A), J5.1, J9.1, U1.2 (IN)
/Buzzer: BZ1.1 (-), U2.24 (D4)
/ESC Left: J20.1, U2.35 (D18)
/ESC Right: J19.1, U2.36 (D23)
/Encoder A: J17.4, U2.22 (D2)
/Encoder B: J17.3, U2.21 (D15)
/Encoder Switch: J17.1, U2.20 (D13)
/FireTrg: J15.2, U2.34 (D5)
/IR Emitter: J24.2, U2.13 (D33)
/IR Rec. Supply: J23.1, U2.12 (D32)
/IR Reciever: JP1.2 (C), U2.11 (D35)
/MagTrg: J16.2, U2.27 (TX2)
/PUSHER PIN: R1.1, U2.14 (D25)
/Preset A: J10.2, J13.3, U2.17 (D14)
/Preset B: J11.2, J13.2, U2.16 (D27)
/Preset C: J12.2, J13.1, U2.15 (D26)
/SCL/SCK (Clock): J18.2, R2.2, U2.39 (D22)
/SDA/SDI (Data): J18.1, R3.2, U2.38 (D19)
GND: BZ1.2 (+), J9.2, J10.1, J11.1, J12.1, J13.4, J14.1, J15.1, J16.1, J17.2, J17.5, J18.4, J19.3, J20.3, Q1.3 (S), R4.1, R5.1, U1.1 (GND), U1.3 (GND), U2.19 (GND)
unnamed: D1.1 (K), J5.2, Q1.2 (D)
unnamed: J23.2, JP1.1 (A), R4.2
unnamed: J23.3, JP1.3 (B)
unnamed: J24.1, R5.2
unnamed: Q1.1 (G), R1.2

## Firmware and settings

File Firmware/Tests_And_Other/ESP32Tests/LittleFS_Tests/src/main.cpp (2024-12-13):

#include <Arduino.h>
#include "FS.h"
#include <LittleFS.h>
#include <time.h>

#include <optional>


/* You only need to format LittleFS the first time you run a
   test or else use the LITTLEFS plugin to create a partition
   https://github.com/lorol/arduino-esp32littlefs-plugin */
   
#define FORMAT_LITTLEFS_IF_FAILED true

void listDir(fs::FS &fs, const char * dirname, uint8_t levels){
    Serial.printf("Listing directory: %s\r\n", dirname);

    File root = fs.open(dirname);
    if(!root){
        Serial.println("- failed to open directory");
        return;
    }
    if(!root.isDirectory()){
        Serial.println(" - not a directory");
        return;
    }

    File file = root.openNextFile();
    while(file){
        if(file.isDirectory()){
            Serial.print("  DIR : ");

            Serial.print(file.name());
            time_t t= file.getLastWrite();
            struct tm * tmstruct = localtime(&t);
            Serial.printf("  LAST WRITE: %d-%02d-%02d %02d:%02d:%02d\n",(tmstruct->tm_year)+1900,( tmstruct->tm_mon)+1, tmstruct->tm_mday,tmstruct->tm_hour , tmstruct->tm_min, tmstruct->tm_sec);

            if(levels){
                listDir(fs, file.name(), levels -1);
            }
        } else {
            Serial.print("  FILE: ");
            Serial.print(file.name());
            Serial.print("  SIZE: ");

            Serial.print(file.size());
            time_t t= file.getLastWrite();
            struct tm * tmstruct = localtime(&t);
            Serial.printf("  LAST WRITE: %d-%02d-%02d %02d:%02d:%02d\n",(tmstruct->tm_year)+1900,( tmstruct->tm_mon)+1, tmstruct->tm_mday,tmstruct->tm_hour , tmstruct->tm_min, tmstruct->tm_sec);
        }
        file = root.openNextFile();
    }
}

void createDir(fs::FS &fs, const char * path){
    Serial.printf("Creating Dir: %s\n", path);
    if(fs.mkdir(path)){
        Serial.println("Dir created");
    } else {
        Serial.println("mkdir failed");
    }
}

void removeDir(fs::FS &fs, const char * path){
    Serial.printf("Removing Dir: %s\n", path);
    if(fs.rmdir(path)){
        Serial.println("Dir removed");
    } else {
        Serial.println("rmdir failed");
    }
}

void readFile(fs::FS &fs, const char * path){
    Serial.printf("Reading file: %s\r\n", path);

    File file = fs.open(path);
    if(!file || file.isDirectory()){
        Serial.println("- failed to open file for reading");
        return;
    }

    Serial.println("- read from file:");
    while(file.available()){
        Serial.write(file.read());
    }
    file.close();
}

void writeFile(fs::FS &fs, const char * path, const char * message){
    Serial.printf("Writing file: %s\r\n", path);

    File file = fs.open(path, FILE_WRITE);
    if(!file){
        Serial.println("- failed to open file for writing");
        return;
    }
    if(file.print(message)){
        Serial.println("- file written");
    } else {
        Serial.println("- write failed");
    }
    file.close();
}

void appendFile(fs::FS &fs, const char * path, const char * message){
    Serial.printf("Appending to file: %s\r\n", path);

    File file = fs.open(path, FILE_APPEND);
    if(!file){
        Serial.println("- failed to open file for appending");
        return;
    }
    if(file.print(message)){
        Serial.println("- message appended");
    } else {
        Serial.println("- append failed");
    }
    file.close();
}

void renameFile(fs::FS &fs, const char * path1, const char * path2){
    Serial.printf("Renaming file %s to %s\r\n", path1, path2);
    if (fs.rename(path1, path2)) {
        Serial.println("- file renamed");
    } else {
        Serial.println("- rename failed");
    }
}

void deleteFile(fs::FS &fs, const char * path){
    Serial.printf("Deleting file: %s\r\n", path);
    if(fs.remove(path)){
        Serial.println("- file deleted");
    } else {
        Serial.println("- delete failed");
    }
}

// SPIFFS-like write and delete file

// See: https://github.com/esp8266/Arduino/blob/master/libraries/LittleFS/src/LittleFS.cpp#L60
void writeFile2(fs::FS &fs, const char * path, const char * message){
    if(!fs.exists(path)){
		if (strchr(path, '/')) {
            Serial.printf("Create missing folders of: %s\r\n", path);
			char *pathStr = strdup(path);
			if (pathStr) {
				char *ptr = strchr(pathStr, '/');
				while (ptr) {
					*ptr = 0;
					fs.mkdir(pathStr);
					*ptr = '/';
					ptr = strchr(ptr+1, '/');
				}
			}
			free(pathStr);
		}
    }

    Serial.printf("Writing file to: %s\r\n", path);
    File file = fs.open(path, FILE_WRITE);
    if(!file){
        Serial.println("- failed to open file for writing");
        return;
    }
    if(file.print(message)){
        Serial.println("- file written");
    } else {
        Serial.println("- write failed");
    }
    file.close();
}

// See:  https://github.com/esp8266/Arduino/blob/master/libraries/LittleFS/src/LittleFS.h#L149
void deleteFile2(fs::FS &fs, const char * path){
    Serial.printf("Deleting file and empty folders on path: %s\r\n", path);

    if(fs.remove(path)){
        Serial.println("- file deleted");
    } else {
        Serial.println("- delete failed");
    }

    char *pathStr = strdup(path);
    if (pathStr) {
        char *ptr = strrchr(pathStr, '/');
        if (ptr) {
            Serial.printf("Removing all empty folders on path: %s\r\n", path);
        }
        while (ptr) {
            *ptr = 0;
            fs.rmdir(pathStr);
            ptr = strrchr(pathStr, '/');
        }
        free(pathStr);
    }
}

void testFileIO(fs::FS &fs, const char * path){
    Serial.printf("Testing file I/O with %s\r\n", path);

    static uint8_t buf[512];
    size_t len = 0;
    File file = fs.open(path, FILE_WRITE);
    if(!file){
        Serial.println("- failed to open file for writing");
        return;
    }

    size_t i;
    Serial.print("- writing" );
    uint32_t start = millis();
    for(i=0; i<2048; i++){
        if ((i & 0x001F) == 0x001F){
          Serial.print(".");
        }
        file.write(buf, 512);
    }
    Serial.println("");
    uint32_t end = millis() - start;
    Serial.printf(" - %u bytes written in %u ms\r\n", 2048 * 512, end);
    file.close();

    file = fs.open(path);
    start = millis();
    end = start;
    i = 0;
    if(file && !file.isDirectory()){
        len = file.size();
        size_t flen = len;
        start = millis();
        Serial.print("- reading" );
        while(len){
            size_t toRead = len;
            if(toRead > 512){
                toRead = 512;
            }
            file.read(buf, toRead);
            if ((i++ & 0x001F) == 0x001F){
              Serial.print(".");
            }
            len -= toRead;
        }
        Serial.println("");
        end = millis() - start;
        Serial.printf("- %u bytes read in %u ms\r\n", flen, end);
        file.close();
    } else {
        Serial.println("- failed to open file for reading");
    }
}

void setup(){
    Serial.begin(115200);
    if(!LittleFS.begin(FORMAT_LITTLEFS_IF_FAILED)){
        Serial.println("LittleFS Mount Failed");
        return;
    }
    
//     listDir(LittleFS, "/", 0);
// 	createDir(LittleFS, "/mydir");
// 	writeFile(LittleFS, "/mydir/hello2.txt", "Hello2");
//   //writeFile(LittleFS, "/mydir/newdir2/newdir3/hello3.txt", "Hello3");
//     writeFile2(LittleFS, "/mydir/newdir2/newdir3/hello3.txt", "Hello3");
// 	listDir(LittleFS, "/", 3);
// 	deleteFile(LittleFS, "/mydir/hello2.txt");
//   //deleteFile(LittleFS, "/mydir/newdir2/newdir3/hello3.txt");
//     deleteFile2(LittleFS, "/mydir/newdir2/newdir3/hello3.txt");
// 	removeDir(LittleFS, "/mydir");
// 	listDir(LittleFS, "/", 3);
//     writeFile(LittleFS, "/hello.txt", "Hello ");
//     appendFile(LittleFS, "/hello.txt", "World!\r\n");
//     readFile(LittleFS, "/hello.txt");
//     renameFile(LittleFS, "/hello.txt", "/foo.txt");
//     readFile(LittleFS, "/foo.txt");
//     deleteFile(LittleFS, "/foo.txt");
//     testFileIO(LittleFS, "/test.txt");
//     deleteFile(LittleFS, "/test.txt");

    listDir(LittleFS, "/", 5);



    readFile(LittleFS, "/settings/settings.json");

	
    Serial.println( "Test complete" );
}

void loop(){


}

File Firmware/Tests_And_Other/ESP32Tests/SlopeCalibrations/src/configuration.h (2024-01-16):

//configuration stuff goes here

#pragma once


//-------------------------------//
//------------outputs------------//
//-------------------------------//

//#define SOLENOID 25 // (HIGH=ON)
#define BUZZER 13 // (HIGH=ON)

//////////////FLYWHEELS//////////////

//use this range to set the min/max values the motor class will take to control the motor, since everything is mapped, values here don't matter too much
//range of valid input
#define FLYWHEEL_SPEED_MIN 0
#define FLYWHEEL_SPEED_MAX 1024 


#define ESC_TYPE_BRUSHED 1 
#define ESC_TYPE_PWM 2 
#define ESC_TYPE_DSHOT 3 

//use the defines above to define this
#define ESC_TYPE ESC_TYPE_DSHOT 

//time in milliseconds between 0 and full before the motor is considered "at speed"
//if ESC_DSHOT_BIDIR is set to true, then this value is ignored
#define ESC_REV_DELAY 1000

//delay in milliseoconds the program should take to decelerate the ESC.
//it hurts both the battery and the ESC to be dropped right to 0 each time the trigger is let off (many ESCs enforce active motor breaking),
//this will slowly ramp down the target speed instead of instantly drop it
//if the motor is brushed, this can be set to 0 (no active breaking there!)
#define ESC_DOWNTHROTTLE_DELAY 3000

//MIN and MAX values for each type of motor output
//for brushed motors, this is the duty cycle of the driver (0-255)
//for PWM escs, this is the angle of the servo (37-180)
//for DSHOT, this is the digital values (default: 48-2047)
#define ESC_OUTPUT_MIN 48 
#define ESC_OUTPUT_MAX 2047 

//the RPM the program expects to get from the motor
//to find most accurate real values for this, motors with telemetry will need to be calibrated
//(can be closely estimated by multiplying kv by voltage)
//for motors without telemetry, these value can be set to anything with decent resolution (to get a "fake" telemetry gauge)
#define ESC_RPM_MIN 0 
#define ESC_RPM_MAX 36800 //39733 //36800 || //29800 //27600 


//only have the option for this if we have the dshot type,
#if ESC_TYPE == ESC_TYPE_DSHOT 
    //dshot mode
    #define ESC_DSHOT_MODE DSHOT300
    //enables eRPM telemetry
    #define ESC_DSHOT_BIDIR true
    //number of magnet poles the motor has, important for getting real RPM from eRPM
    #define ESC_DSHOT_MOTOR_POLES 14
#endif


//esc pinouts
#define ESC_1_PIN 18
#define ESC_2_PIN 23

//#define FOUR_ESCS
#ifdef FOUR_ESCS
    #define ESC_3_PIN
    #define ESC_4_PIN
#endif

//////////////PUSHER//////////////

//the range of input (full speed = PUSHER_SPEED_MAX)
#define PUSHER_SPEED_MAX 1024
#define PUSHER_SPEED_MIN 0

#define PUSHER_TYPE_BRUSHED 0 //not implemented
#define PUSHER_TYPE_STEPPER 1 //not implemented
#define PUSHER_TYPE_SOLENOID 2
#define PUSHER_TYPE_NULL 3

//set the pusher type here
#define PUSHER_TYPE PUSHER_TYPE_SOLENOID

//set the corresponding defines here. you only need to touch the ones that correspond with PUSHER_TYPE
//PUSHER_TYPE_BRUSHED
//the two pins on the h bridge driver
#define H_A_PIN -1
#define H_B_PIN -1

//PUSHER_TYPE_STEPPER
//the pins that control the stepper driver
#define S_STEP_PIN -1
#define S_ENABLE_PIN -1
#define S_DIRECTION_PIN -1


//PUSHER_TYPE_SOLENOID
//the pin that controls the solenoid FET
#define SO_FET_PIN 32 //use buzzer for testing
//time in ms it takes the solenoid to extend
#define SO_MIN_EXT_TIME 25
//time in ms it takes the solenoid to retract
#define SO_MIN_RET_TIME 25
//max time the solenoid is allowed to be ON
#define SO_MAX_EXT_TIME 200



//------------------------------//
//------------inputs------------//
//------------------------------//


//////////////buttons//////////////
//all buttons will use internal pullup resistors by default

//debounce time in ms
#define DEBOUNCE_TIME 10

//the pin that this element occupies
#define TRIGGER_PIN 17
//if normally closed, set this to true, if normally open, set to false
#define TRIGGER_NC false

#define MAG_TRIG_PIN 5
#define MAG_TRIG_NC false

//do we have a rev trigger in the mix? if yes, we change the way some rev behavior works
//TODO: implement this.
//#define USE_REV_TRIG
#ifdef USE_REV_TRIG
  #define REV_TRIG_PIN 16
  #define REV_TRIG_NC false
#endif

//preset buttons
#define PRESET_A_PIN 27
#define PRESET_A_NC false

#define PRESET_B_PIN 14
#define PRESET_B_NC false

#define PRESET_C_PIN 12
#define PRESET_C_NC false

//encoder pins for the UI interaction
#define ENCODER_A_PIN 25
#define ENCODER_B_PIN 33

#define ENCODER_BUTTON_PIN 26
#define ENCODER_BUTTON_NC false


//////////////ammo counter//////////////
//voltage+ pin for the reciever diode (not absolutely needed, but saves power as it is only set ON when it is time to read)
#define IR_REC_POWER 15
//other side of the diode, measures IR light level
#define IR_REC_READBACK 35
//IR emitter LED, not absolutely needed, but it saves wear on the LED and battery if used
#define IR_EMITTER 2
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

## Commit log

2023-06-04 CAD -woot woot
    I think I know what it's going to look like...
2023-06-05 more cad work, added ESC music
    simple as that.
    [Solenoid.SLDPRT, Solenoid.STL]
2023-06-10 basic blaster is almost done
    currently, it's a box, but a functional box...
2023-06-14 CAD updates
    Added screw holes to everything...
2023-06-20 Lots of CAD
    [BatteryTray.stl, FlywheelCageHalf.stl, FlywheelCoverLeft.stl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]
2023-06-21 heavy cad work
    [BrushlessMotorMount.stl, FlywheelCapBottom.stl, FlywheelCapLeft.stl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]
2023-06-23 more CAD work, very close to finished product
    I failed to meet the deadline, but I came darn close
    [BrushlessMotorMount.stl, ButtonHolder.stl, ElectronicsCap.stl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]
2023-06-23 created the G4 PCB
    all of it.
    [G4_Controller_Board.kicad_pcb, G4_Controller_Board.kicad_sch, G4_Controller_Board_Wide_Layout.kicad_pcb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]
2023-07-11 working on software
    ported FDL3 software to platformIO (for reference only)
    [G4_Controller_Board.kicad_sch]
2023-07-11 CAD
    exported to STL for printing, made some model tweaks as problems were found
    [BackSideCover.stl, BrushlessMotorMount_Alt.stl, FlywheelHoleSizeTest.stl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]
2023-07-22 Programming work
    Trying to get d-shot bidirectional working on an ESP32
    [CONFIGURATION.h, Configuration.h, Dettlaff_Core_v0.1.step]
2023-08-09 firmware updates
    started work on "detty"
    [CONFIGURATION.h, configuration.h]
2023-08-14 updated controller board schematics
    [G4_Controller_Board.kicad_sch]
2023-08-21 work on Detty
    working with menu UI
    [configuration.h]
2023-08-22 UI work
    integrating menus and gauges into the firmware
    [configuration.h]
2023-08-23 working with the draw code
    had to add a timed interrupt in order to update the input quickly enough in light of the u8g2 code
2023-08-26 implement basic menu
    used the GEM-Breakout library and fixed some other bugs
    [main.cpp]
2023-08-29 more firmware work
    began work on settings
    [configuration.h]
2023-09-05 begin work on connectome
    fixed flywheel and solenoid backends
    [configuration.h]
2023-09-07 more firmware updates
    select fire and cache behavior created
    [DartFinger.3mf, DartFinger.stl, configuration.h]
2023-09-08 add basic full auto
    currently does not acknowledge trigger type
    [configuration.h]
2023-09-14 firmware and hardware revisions
    need to beef up flywheels and redesign electronics bay
    [FrontSideCover.stl, configuration.h]
2023-09-28 CAD updates
    working on new flywheel cage design
2023-09-29 CAD updates
2023-10-12 update CAD
2023-10-15 work on newer board revision
    spitting into 2 boards to make the design both more compact and robust
    [FastDecayDriver.kicad_pcb, FastDecayDriver.kicad_sch, G4_Controller_Board.kicad_pcb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]
2023-10-17 begin work on new PCB
    2 layers with fast decay driver
    [FastDecayDriver.kicad_sch, G4_Controller_Board.kicad_pcb, G4_Controller_Board.kicad_sch]
2023-10-17 update the PCB
    added more traces
    [G4_Controller_Board.kicad_pcb, G4_Controller_Board.kicad_sch]
2023-10-19 update PCB model
    progress on logic-side board
    [G4_Controller_Board.kicad_pcb, G4_Controller_Board.kicad_sch, LOLIN32 pinLabels.kicad_sch]
2023-10-20 update kicad schematic
    [G4_Controller_Board.kicad_sch]
2023-10-23 try 3 flywheel mount
    tried single piece flywheel mount, but that resulted in print issues, so I'm trying a different method that uses more bolts. Also updated other things such as the PCB.
    [BrushlessMotorMount.stl, BrushlessMotorMount_Alt.stl, CageMotorMount.stl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]
2023-10-23 more work on front cage (small work)
    [CageHalf.stl]
2023-10-28 update PCB
    prototype revision should be completed
    [G4_Controller_Board.kicad_pcb, G4_Controller_Board.kicad_sch]
2023-10-31 Last save of 2 board setup
    current boards integrate half-bridge and IO buttons on the same PCB, with the ESP32 on the other one. I'm considering splitting the encoder and buttons off into their own floating PCB, leaving more r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
    [G4_Controller_Board.kicad_pcb]
2023-11-02 update PCB
    trying 3 PCB config (floating buttons, ESP32, and fast decay driver)
    [G4_Controller_Board.kicad_pcb, G4_Controller_Board.kicad_sch]
2023-11-02 add updated CAD files
    oops, this should have been with the last commit!
2023-11-03 update PCB traces
    [G4_Controller_Board.kicad_pcb, G4_Controller_Board.kicad_sch]
2023-11-05 create machine code for PCB
    nc code generated to machine out the physical PCB tests
    [G4_Controller_Board.kicad_pcb, G4_Controller_Board.kicad_sch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]
2023-11-06 CAD and CNC updates
2023-11-09 CAD updates
    add models of controller board to SKP
2023-11-10 decay driver test code and updated CAD
    what it says on the tin
2023-11-11 shift files
    [BackSideCover.stl, ElectronicsCap.stl, NooseMount.stl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]
2023-11-22 CAD updates
    approaching finished product
    [BottomLEDCap.stl, CageHalf.stl, CircuitWall.stl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]
2023-11-23 work on firmware
    attempting to add task scheduling and chronometer
    [CONFIGURATION.h, Configuration.h, Dettlaff_Core_v0.1.step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]
2023-11-27 firmware upsates
    add more support for ammo counter, still not working
    [configuration.h]
2024-01-16 split Detty into 2 sub-types
    synchro-detty doesn't use task scheduling, while async-detty does
    [FlywheelSpeedScatter.xlsx, Sloper.xlsx, configuration.h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]
2024-01-21 !Statistics!
    How fun
    [old_speed_200.csv, old_speed_300.csv, old_speed_400.csv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]
2024-08-29 split detty into its own repository
    [CONFIGURATION.h, Dettlaff_Core_v0.1.step, configuration.h]
2024-12-13 tests for g4 firmware
    [min_littlefs.csv]
